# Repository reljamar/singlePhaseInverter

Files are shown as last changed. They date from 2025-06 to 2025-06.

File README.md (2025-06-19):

# singlePhaseInverter
*Precursor project to a future three-phase inverter for driving synchronous motors. This project is a work in progress.*

## Purpose
This project is aimed to provide experience a rounded engineering exercise. It blends hardware development for power electronics with inverter control algorithms and time-sensitive embedded software on which the algorithm runs.
After the single-phase inverter is reliable operating with a control loop, a new 3-phase inverter project will be started, with an ultimate goal of reducing inverter conduction and switching losses.

## Description
A low-voltage, single phase inverter system, controlled by an STM32 G431 microcontroller. The PCB, algorithm, and control software are self-developed but based on existing design practices. The inverter contains 4 power switching transistors, an array of DC link capacitors, four gate drivers, a precharge function for the DC link, two current measurment shunts, and one hall current sensor. The design purposely uses:
- multiple large capacitors to allow for trying out various capacitor types and values;
- multiple current sensing types to allow experimenting with each approach
- multiple different shunt amplifier types, again for experimenting purposes
- low voltage, for safety reasons
- through-hole transistors with a large thermal overhead
All of these choices were made primarily to simplify the development of the control algorithm, and with locally available components. After a stable algorithm is established, a new version of hardware can be developed to optimize DC link size and type, transistor size, gate driver selection, current and voltage measurement, and overall BOM cost.
The inverter is purposly made low-voltage, primarily for safety reasons, but also to lower costs and save time on isolation coordination.

<p align="center">
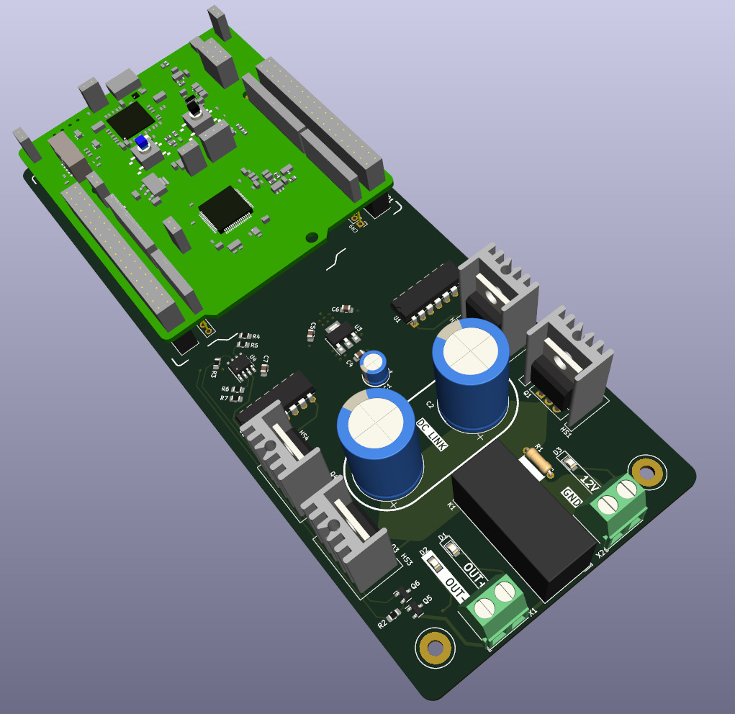
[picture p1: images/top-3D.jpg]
3D model

</p>

## Overview
- Discrete H-bridge circuit
- Serial port debugging
- Variable frequency control

## Project status
Currently the project performs fixed frequency PWM control of the transistors at a very low switching frequency of 10kHz - this is done to minimize complications that arise from higher switching frequencies. The output waveform frequency is 60Hz. Due to such a low switching frequency, in order to keep the current low, the output is loaded with a large, custom-made 22mH inductor for smoothing the waveform. Currently the issue is for very small and very large pulse widths, the gate driver cannot properly drive the switching transistors.

<p align="center">
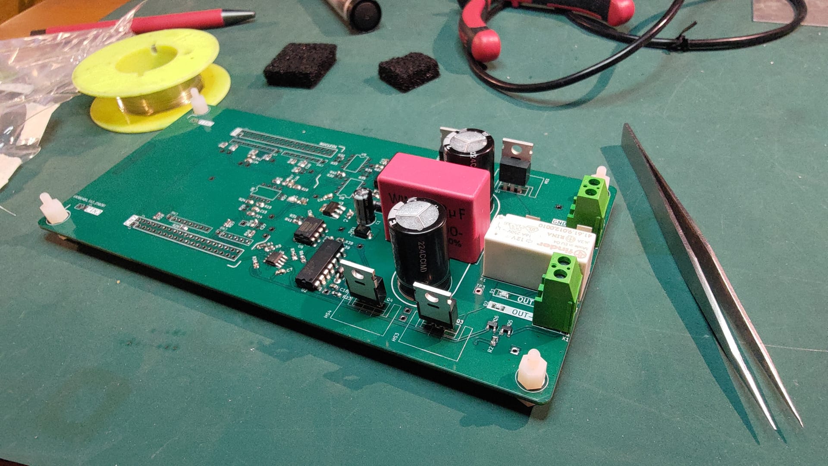
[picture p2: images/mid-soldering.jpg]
Soldering

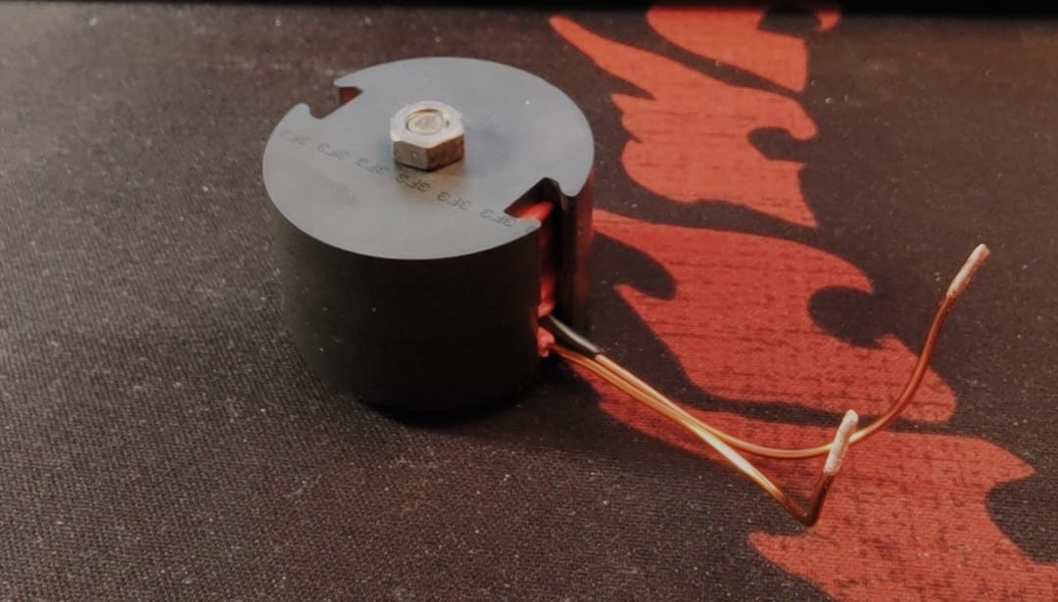
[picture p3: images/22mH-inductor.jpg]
inductor

</p>

## System architecture

<p align="center">
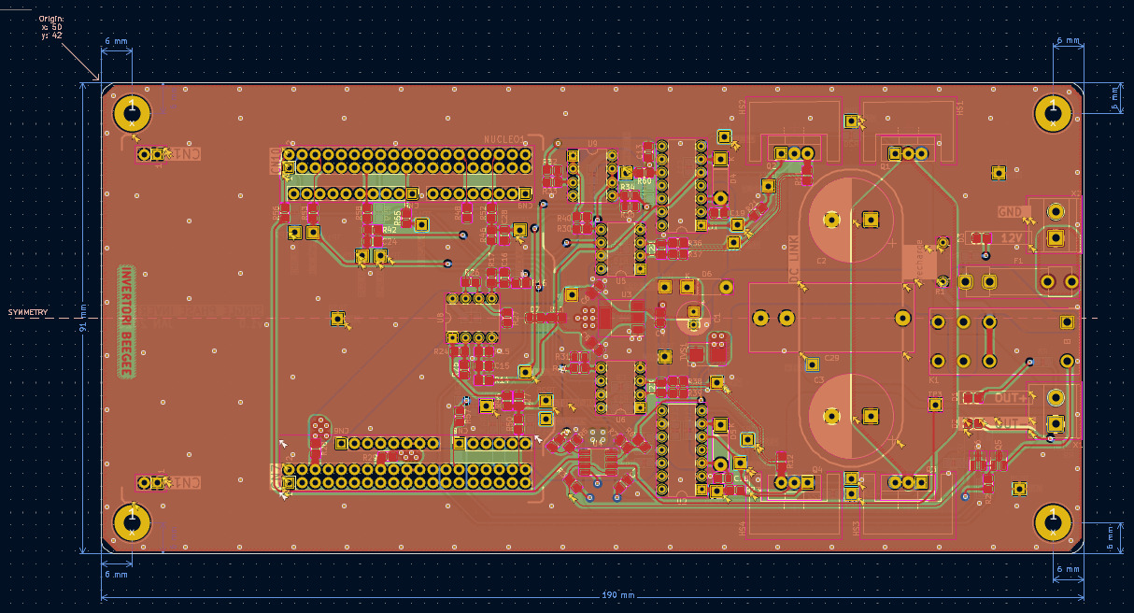
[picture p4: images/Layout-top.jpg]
Layout

</p>

### Microcontroller
The system is based on an STM32 G431 microcontroller. In this first version of the hardware, a NUCLEO development board is used for the actual MCU implementation, to save on development time. The output of the MCU are four PWM signals, one for driving each transistor, generated in the MCU's internal timers, and include a 1% dead-time between complementary signals. The MCU also controls the precharge.
### H-bridge
The inverter in this phase uses four IRF540N transistors. These transistors are much larger than necessary, and no heat sink is needed. The transistors are driven by two IR2113 gate drivers. The DC link capacitor currently in use is oversized, and will be optimized in a future version.
### Current and voltage measurement
The DC voltage, as well as the both AC outputs are measured through resistor deviders. The current is measured in multiple locations, and the optimal current sensor will be chosen. A shunt resistor is located on the source of the low-side transistor on each H-bridge branch. The small voltage across the shunt is amplified to a MCU-readable via an instrumentation amplifier. Two different instrumentation amplifiers are used for each shunt resistor, and the more appropriate one will be chosen to be implemented on both shunts. They are pin-compatible. The current is also measured on one of the output lines (in theory, only this current is needed for control).
### Precharge
Precharge is needed due to the large DC link capacitance. A single-pole, double throw relay is used for precharge. Without power or an active control signal, the relay connects the DC link voltage to the input DC voltage through a 100-ohm resistor. Once the DC link voltage reaches 90% of the input DC voltage, the relay switches to its other output, which directly connects the input and DC link potential. The entire inverter current passes through this relay.
### Control
The current status of the project implements a fixed PWM signal, where the pulse width for each period is read out of a pre-calculated lookup table. The final control algorithm will implement a simple PI controller. The controller is simulated in Simulink.
## Firmware
### Implemented features
- [x] PWM signal generated from predetermined lookup table
- [x] Serial interface debugging
- [x] Timer PWM and deatime control
- [x] Reliable analog current and voltage readings - _work in progress_
### Planned features
- [ ] PI controller implemented in firmware
- [ ] Real-time Pulse Width calculation

## Future improvements
Once the entire project is working reliable, more advanced features can be implemented:
- Soft start
- Dithering

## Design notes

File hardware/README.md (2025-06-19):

This folder contains the KiCAD project files for the first PCB version.
There are four schematic pages:
1. Root page - top overview page. Displays how the individual sheets are connected, and contains some high-level elements such as mounting holes and input/output connectors;
2. Control page - contains the MCU and precharge control elements;
3. Power page - contains everything related to the high-power part of the inverter: the H-bridge, gate drivers, precharge relay, shunt resistors;
4. Measure page - contains all circuits used for measuring voltages and currents: voltage deviders, amplifiers, offsets, filters.

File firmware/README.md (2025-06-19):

The firmware is not yet in a stage where it can be publicly presented.
